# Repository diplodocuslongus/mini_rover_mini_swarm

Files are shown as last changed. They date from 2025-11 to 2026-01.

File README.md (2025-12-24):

# Mini rover mini swarm

Using the pololu romi platform to create a swarm of few rovers.
Documenting the assembly, setup and usage of some simple, basic and more or less cheap rover platform such as the pololu romi to be controlled by an autopilot (ex ardurover) and evolve in a swarm.

## Rover platform

For all options (pololu romi or alternatives):
- autopilot board compatible with the chosen autopilot (ardupilot or PX4), we chose the mateksys F405-WMO, the [h743-mini](https://www.mateksys.com/?portfolio=h743-mini) is fine too.

### Romi

BOM (can be adjusted)
- romi chassis
- [power distribution](https://www.pololu.com/product/3541) board or the [motor driver + power board](https://www.pololu.com/product/3543) or the [controller board](https://www.pololu.com/product/3544) 
- [encoder pair for romi motors ](https://www.pololu.com/product/3542)
- NiMH batteries
- motor driver (if not using the controller board)

[Assembly guide:](https://www.pololu.com/docs/0J68/all)

Other references:
- https://ardupilot.org/rover/docs/common-autopilots.html
- https://discuss.ardupilot.org/t/ardurover-with-the-pololu-romi/41991

### Cheap platform

Similar outcomes can be achieved with various degrees of success by using cheap platform, but they may be unrelieable especially when it comes to the wheel encoder parts. 

## autopilot

### control modes

The [follow mode](https://ardupilot.org/rover/docs/follow-mode.html) can be used for a basic swarm like behaviour, though it doesn't include any form of self-decision: vehicles follow each other and in order, with one vehicle in front.

### Firmware

This page says to use this firmware:
https://www.mateksys.com/?portfolio=f405-wmo#tab-id-2

https://firmware.ardupilot.org/Rover/stable/MatekF405-TE/

## connections

Power distribution board
By dfault the power distribution board supplies voltage from all the 6 batteries of the ROMI, this can be changed but having enough voltage is best to power directly the autopilot.

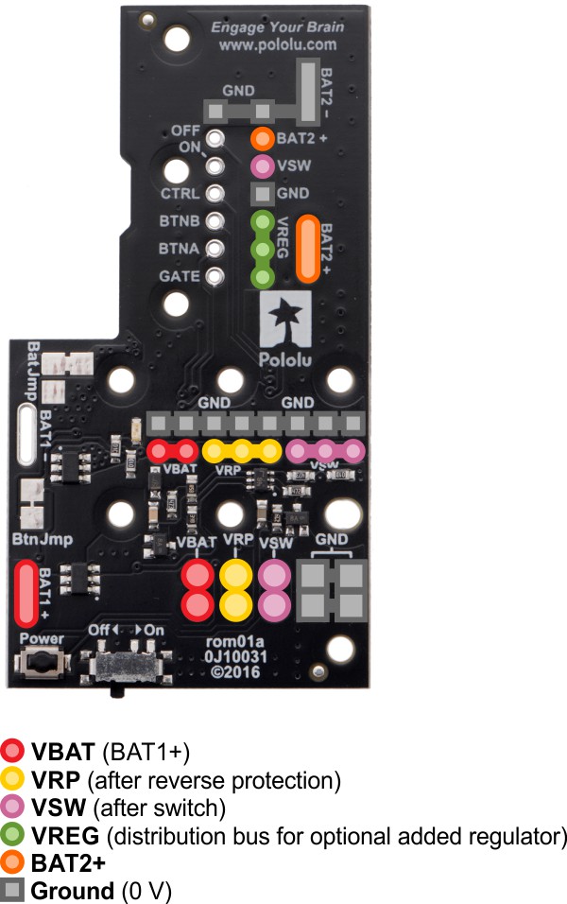
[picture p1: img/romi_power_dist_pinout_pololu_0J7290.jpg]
power_dist_pinout


**Wheel encoder.**

VCC can be 3.5 V to 18 V

*Important*
The Mateksys F405-WMO flight controller does not have physical, onboard pull-up resistors, neither does the wheel encoder for ROMI. They must be installed or the wheel encoder signal will be too weak for the FC to detect it.
Solder 4.7k resistor between the output A and B and VCC for each encoder.
That is, one 4.7k resistor from output A to VCC and another 4.7k from output B to VCC for left encoder, repeat for the right one.

https://ardupilot.org/rover/docs/wheel-encoder.html

Connect the encoder VCC to one of the Vx pin on the autopilot.

The AP we use has 3.3V logic levels but it is 5V tolerant.

Motor driver

It requires 2 separate supplies, one to the logic (1.8V ~ 7V) and one for the power to the motors (2~11V). The logic voltage can be obtained from the autopilot, or via a voltage converter.

Note that the motors are positioned in a mirror image of each other so if connecting everything exactly on the left and right, motors will spin in opposite directions when increasing the throttle. If this happens, simply inverse M1 with M2 on one of the encorder board (or on the driver output).
The same concept goes if motors are spinning in reverse (rover moving forward when it should move backward).

**RC receiver.**

A futaba receiver was used and pairing and connection varies depending on the RC brand and protocol.

This is an sbus based Rx, connect to the mateksys to the SBUS pin, and a 5V power pin such as Vx or the 4V5 pin which is powered when the FC is connected to USB to a computer.

## Autopilot setup

Calibrate the radio in QGC or MP.

Setup the various parameters

Everytime one or more parameters is set, the FC has to be rebooted in order for the parameter to be taken into account.
For example in a newly flashed FC, RELAYx_FUNCTION is set to 0 and no other RELAY related parameters will appear.
In order to access to other RELAY parameters such as RELAYx_PIN, etc, the RELAYx_FUNCTION has to be set and the FC rebooted.

We will use the motor driver in phase-enable mode (in motor driver language; ithis corresponds to "brushed with relay" in the ardupilot [wiki](https://ardupilot.org/rover/docs/common-brushed-motors.html#common-brushed-motors)), and the connections follows the schematic from pololu.
"Brushed With Relay” is for brushed motor drivers that use a relay pin to indicate whether it should rotate forward or backward. 

The type of control for the romi is called skid steering. The settings below are made for this.

https://ardupilot.org/rover/docs/rover-motor-and-servo-configuration.html#skid-steering

Summary of all settings

RELAY1_FUNCTION -> 5
RELAY1_PIN -> 50
RELAY2_FUNCTION -> 6
RELAY2_PIN -> 51

WENC_TYPE -> 1 (quadrature)
WENC2_TYPE -> 1 (quadrature)

# MOT_PWM_TYPE

MOT_PWM_TYPE -> 3 (BrushedWithRelay)

*SERVO*

Servo parameters dictates whether a given pin acts as PWM or GPIO.
They must be set properly.

See below for how to set them on a per-function basis.

*RELAY_FUNCTION*

Relay are used to select the rotation direction of the motors on the motor driver.
Search for relay in the search box of QGC or MP.
Set as follows:

RELAY1_FUNCTION -> 5
RELAY2_FUNCTION -> 6

For this to work we also have to set the corresponding servo function to GPIO:

SERVO7_FUNCTION -> -1 (GPIO)
SERVO8_FUNCTION -> -1 (GPIO)

Reboot

Then set relay pins:
RELAY1_PIN -> 56
RELAY2_PIN -> 57

[!] The value for these parameters is HW dependent, check the FC datasheet and double check with the hwdef.dat file corresponding to that particular FC.
Note also that these are connected to S1 and S2 pins on the FC. 
[!] it is adviced not to mix pins dedicated to GPIO (ex, relay function) and pins dedicated to PWM.

For the MatekSys F405-WMO, the corresponding hwdef.dat is [here](https://github.com/ArduPilot/ardupilot/blob/master/libraries/AP_HAL_ChibiOS/hwdef/MatekF405-TE/hwdef.dat)

*WENC (Wheel encoder)*

Related [ardurover doc](https://ardupilot.org/rover/docs/wheel-encoder.html).
set WENC_TYPE  to 1 (quadrature) and reboot the FC to enable other parameters and the second wheel encoder.

WENC_TYPE -> 1 (quadrature)

reboot so that more parameters and the second wheel encoder appears.

WENC2_TYPE -> 1 (quadrature)

Set the corresponding servo function to GPIO:

SERVO3_FUNCTION -> -1 (GPIO)
SERVO4_FUNCTION -> -1 (GPIO)
SERVO5_FUNCTION -> -1 (GPIO)
SERVO6_FUNCTION -> -1 (GPIO)

set EK3_SRC1_VELXY to 7 (WheelEncoder)

## command the rover with mavlink messages

### using mavproxy

Install mavproxy

Turn on the main power , plug the FC usb to the computer.

    mavproxy.py --master=/dev/ttyACM0 --baudrate=115200

Open with the console

    $ mavproxy.py --master=/dev/ttyACM0 --baudrate=115200 --console

To connect via an AP, see picoW AP code, use:

    mavproxy.py --master=udpout:192.168.4.1:14550

`192.168.4.1` is the picoW's IP address and `14550` the port for udp

Lots of messages will be shown in the console, which can be inconvienient when typing malink commands, so send these message to the gui console by typing:

    module load console

Or load mavproxy with the console module directly:

    mavproxy.py --master=udpout:192.168.4.1:14550 --console

Make sure EK3_SRC1_VELXY is set to 7 (to make use of wheel odometry)

Either in QGC or using a mavlink message:

params set ek3_src1_velxy 7 

(tip: tab completion works, and if the parameter's name is unsure, type:

`param set ek3_src1*`, which will show:

    EK3_SRC1_POSXY   0           # None
    EK3_SRC1_POSZ    0           # None
    EK3_SRC1_VELXY   7           # WheelEncoder
    EK3_SRC1_VELZ    0           # None
    EK3_SRC1_YAW     0           # None

We need to set the GPS origin:

    module load message
    message SET_GPS_GLOBAL_ORIGIN 0 -353621474 1491651746 600000 0

Change to guided mode and arm:

    mode guided
    arm throttle

Then send a move forward message:

    message SET_POSITION_TARGET_LOCAL_NED 0 0 0 7 3580 0.6 0 0 0 0 0 0 0 0 0 0

Simple test: spin the wheels for a given distance or velocity:

Ensure 

### using program (C or python)

A program is used to send specific commands.

Python:

1) connect to the pico W AP
2) connect to rover with :

    mavproxy.py --master=udpout:192.168.4.1:14550

3) in mavproxy, run:

        module load console
        module load message
        message SET_GPS_GLOBAL_ORIGIN 0 -353621474 1491651746 600000 0
        mode guided
        arm throttle

4) run the python script to move forward:
    
    py move_fwd.py

## send telemetry via a companion computer.

We chose the raspberry pi picoW for this.

We'll set up a full MAVLink communication between the rover and QGroundControl (QGC) using the Raspberry Pi Pico W as a UDP bridge.

- Integrate MAVLink into the Pico W code (to encode/decode MAVLink messages).
- Forward MAVLink messages between the flight controller (FC) and QGC via UDP.
- Ensure QGC is configured to connect to the Pico W's UDP endpoint.

## Useful references:

- [list of all rover parameters](https://ardupilot.org/rover/docs/parameters.html)
- 

## Abreviations

AP: AutoPilot (=FC)
FC: Flight controller

# Debugging

## general guidelines

Monitor some parameters in mavproxy

    watch name_of_the_parameter

stop watching (this will stop watching everything):

    watch clear 

For one shot watching all the parameters:

    status 

For a single parameter, here to see the RC channels as read by the FC (needs RC on and connected of course to see a change):

    status RC_CHANNELS

## rover moves backward

General guideline: leave the RC channels as they are on the RC itself, i.e. don't reverse them there, and reverse what is required on the FC parmaeters.

Reverse in AP if needed (RC3 is throttle here, check setting)

    param set RC3_REVERSED 1 

## rover moves too fast

Check the following FC parameters:

    param show CRUISE_SPEED
    param show WP_SPEED

Lower the values for CRUISE_SPEED and WP_SPEED (values are in m/s).

## Rover spinning on itself

- check motor direction
- `SERVOx_REVERSE`: normal or reversed? (x = 1 and 2 in this setup)
- check if RC can normally control the Rover
-
Check the values of the steering rate controller (ex, from mavproxy)

    param show ATC_STR_RAT_*
    GUIDED> ATC_STR_RAT_D    0.0
    ATC_STR_RAT_D_FF 0.0
    ATC_STR_RAT_FF   0.20000000298023224
    ATC_STR_RAT_FLTD 0.0
    ATC_STR_RAT_FLTE 10.0
    ATC_STR_RAT_FLTT 0.0
    ATC_STR_RAT_I    0.20000000298023224
    ATC_STR_RAT_IMAX 1.0
    ATC_STR_RAT_MAX  120.0
    ATC_STR_RAT_P    0.20000000298023224
    ATC_STR_RAT_PDMX 0.0
    ATC_STR_RAT_SMAX 0.0

Some parameters that affect the turn and turn rate:

    param set ATC_STR_RAT_MAX 30
    param set ATC_STR_RAT_FF 0.3
    param set MOT_SLEWRATE 60
    param set MOT_THR_MIN 10

## rover tends to veer on one side when moving forward

Adjust with SERVO1_TRIM andi/or SERVO2_TRIM.

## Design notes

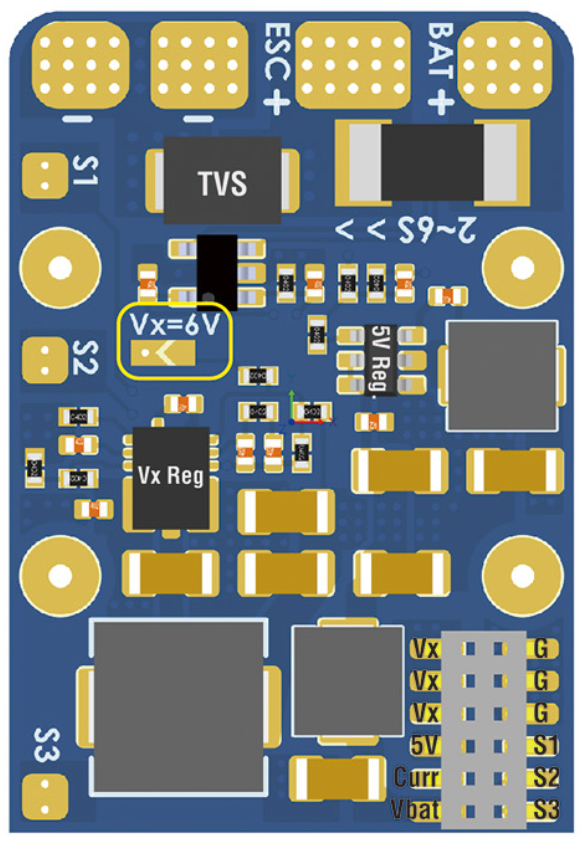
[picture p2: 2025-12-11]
img/mateksysF405_wmo_bottom.png

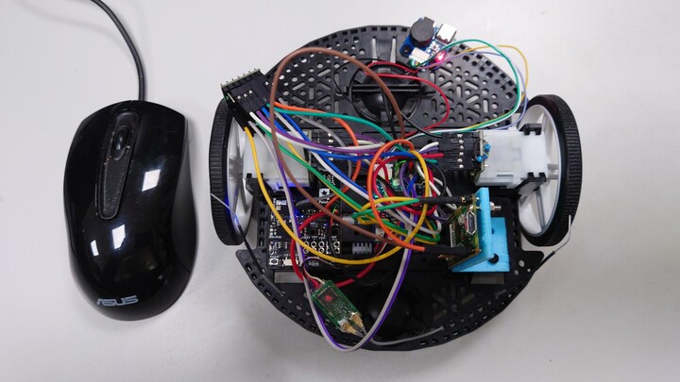
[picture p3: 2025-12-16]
img/romi_rover_picoW.jpg

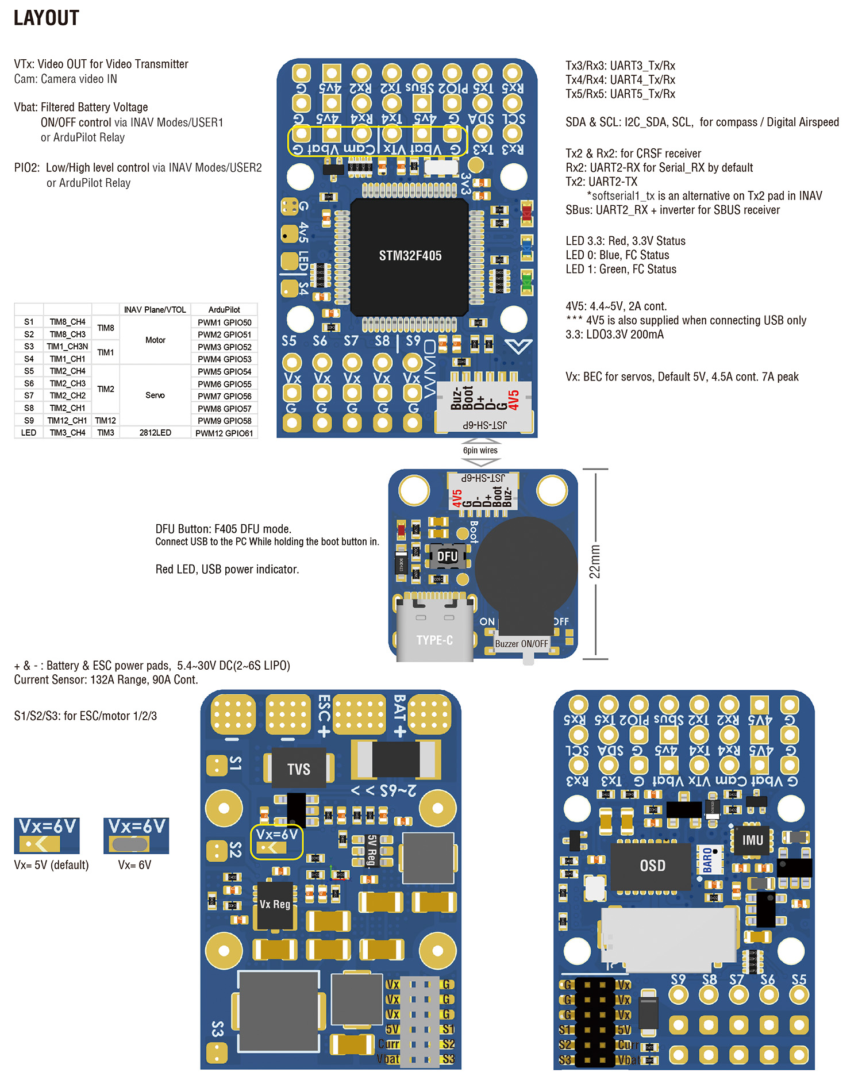
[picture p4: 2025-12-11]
img/mateksysF405-WMO_layout.jpg

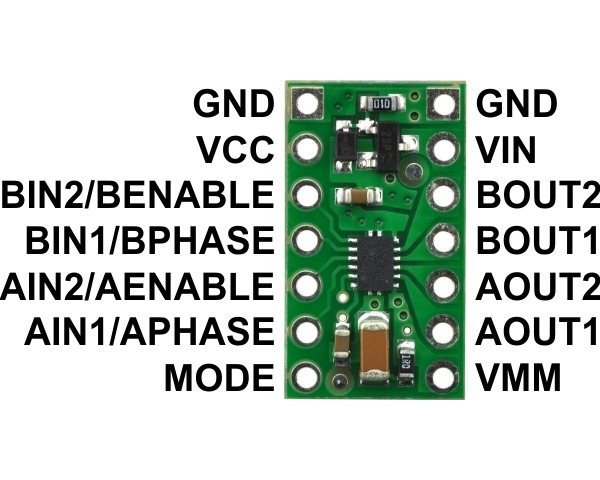
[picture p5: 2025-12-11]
img/pololu_motor_driver_drv8835.jpg

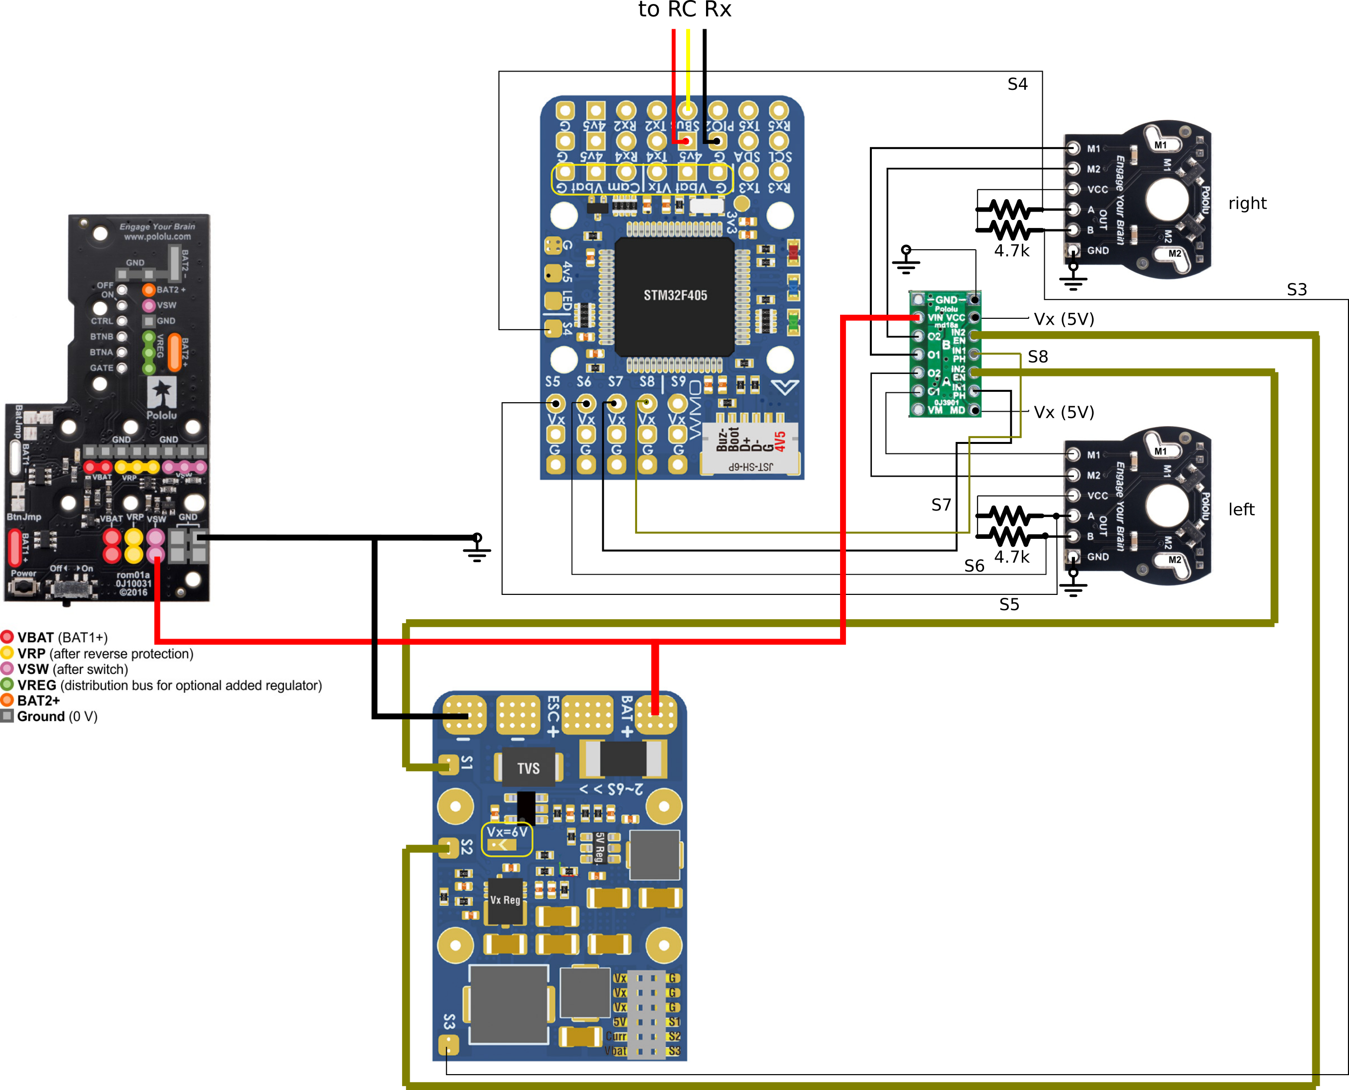
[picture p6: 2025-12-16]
img/all_connections_no_picow.png

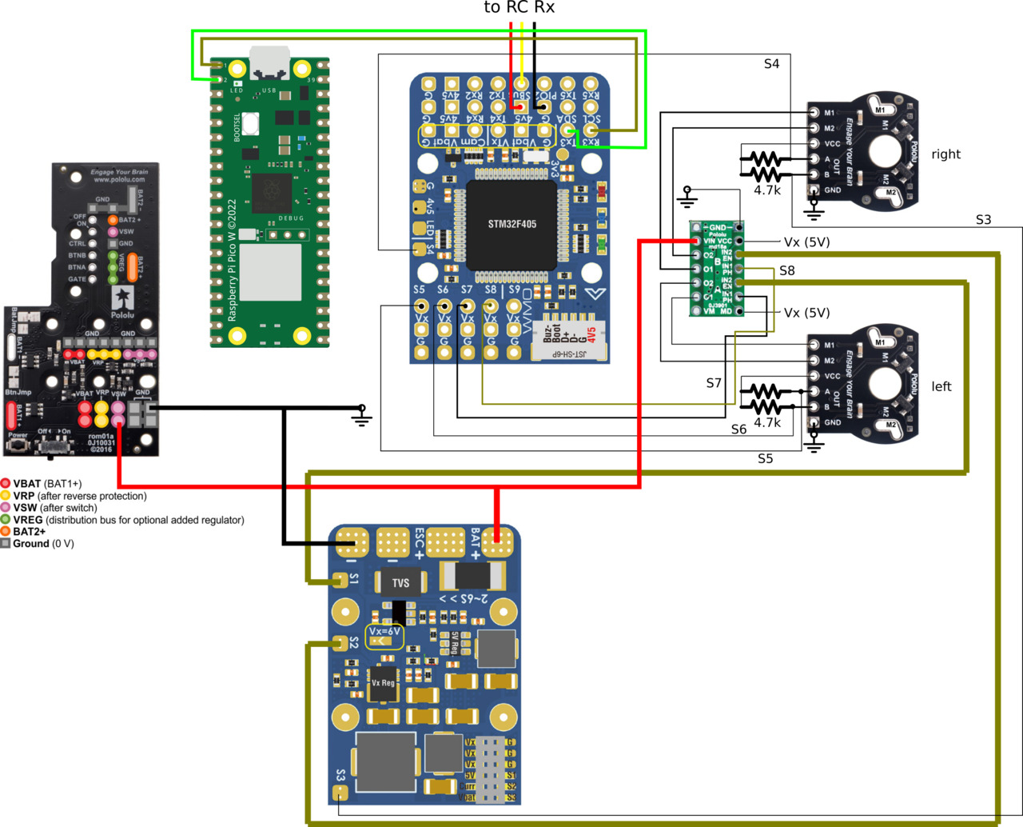
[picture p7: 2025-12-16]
img/all_connections_picow.jpg

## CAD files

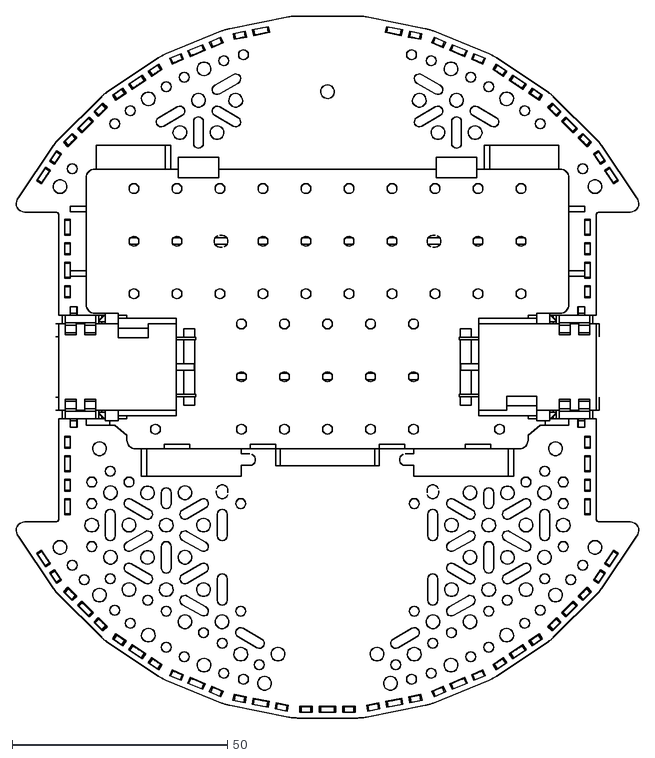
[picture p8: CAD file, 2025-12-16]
img/romi_chassis_toponly_nowheels_fromdxf.dxf
144.8 x 163.2

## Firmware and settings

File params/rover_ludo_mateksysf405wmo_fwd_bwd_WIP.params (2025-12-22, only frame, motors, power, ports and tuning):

1	1	ATC_SPEED_D	0.000000000000000000	9
1	1	ATC_SPEED_D_FF	0.000000000000000000	9
1	1	ATC_SPEED_FF	0.000000000000000000	9
1	1	ATC_SPEED_FLTD	0.000000000000000000	9
1	1	ATC_SPEED_FLTE	10.000000000000000000	9
1	1	ATC_SPEED_FLTT	0.000000000000000000	9
1	1	ATC_SPEED_I	0.200000002980232239	9
1	1	ATC_SPEED_IMAX	1.000000000000000000	9
1	1	ATC_SPEED_P	0.200000002980232239	9
1	1	ATC_SPEED_PDMX	0.000000000000000000	9
1	1	ATC_SPEED_SMAX	0.000000000000000000	9
1	1	ATC_STR_ACC_MAX	20.000000000000000000	9
1	1	ATC_STR_ANG_P	2.000000000000000000	9
1	1	ATC_STR_RAT_D	0.000000000000000000	9
1	1	ATC_STR_RAT_D_FF	0.000000000000000000	9
1	1	ATC_STR_RAT_FF	0.200000002980232239	9
1	1	ATC_STR_RAT_FLTD	0.000000000000000000	9
1	1	ATC_STR_RAT_FLTE	10.000000000000000000	9
1	1	ATC_STR_RAT_FLTT	0.000000000000000000	9
1	1	ATC_STR_RAT_I	0.000000000000000000	9
1	1	ATC_STR_RAT_IMAX	1.000000000000000000	9
1	1	ATC_STR_RAT_MAX	120.000000000000000000	9
1	1	ATC_STR_RAT_P	0.200000002980232239	9
1	1	ATC_STR_RAT_PDMX	0.000000000000000000	9
1	1	ATC_STR_RAT_SMAX	0.000000000000000000	9
1	1	BATT2_MONITOR	0	2
1	1	BATT3_MONITOR	0	2
1	1	BATT4_MONITOR	0	2
1	1	BATT5_MONITOR	0	2
1	1	BATT6_MONITOR	0	2
1	1	BATT7_MONITOR	0	2
1	1	BATT8_MONITOR	0	2
1	1	BATT9_MONITOR	0	2
1	1	BATT_AMP_OFFSET	0.000000000000000000	9
1	1	BATT_AMP_PERVLT	66.699996948242187500	9
1	1	BATT_ARM_MAH	0	6
1	1	BATT_ARM_VOLT	0.000000000000000000	9
1	1	BATT_CAPACITY	3300	6
1	1	BATT_CRT_MAH	0.000000000000000000	9
1	1	BATT_CRT_VOLT	0.000000000000000000	9
1	1	BATT_CURR_PIN	15	2
1	1	BATT_FS_CRT_ACT	0	2
1	1	BATT_FS_LOW_ACT	0	2
1	1	BATT_FS_VOLTSRC	0	2
1	1	BATT_LOW_MAH	0.000000000000000000	9
1	1	BATT_LOW_TIMER	10	2
1	1	BATT_LOW_VOLT	0.000000000000000000	9
1	1	BATT_MONITOR	4	2
1	1	BATT_OPTIONS	0	6
1	1	BATT_SERIAL_NUM	-1	6
1	1	BATT_VLT_OFFSET	0.000000000000000000	9
1	1	BATT_VOLT_MULT	21.000000000000000000	9
1	1	BATT_VOLT_PIN	14	2
1	1	FLTMODE_GCSBLOCK	0	6
1	1	FRAME_CLASS	1	2
1	1	FRAME_TYPE	0	2
1	1	INS_GYRO_FILTER	4	4
1	1	INS_HNTCH_ENABLE	0	2
1	1	MOT_PWM_FREQ	16	2
1	1	MOT_PWM_TYPE	3	2
1	1	MOT_SAFE_DISARM	0	2
1	1	MOT_SLEWRATE	100	4
1	1	MOT_SPD_SCA_BASE	1.000000000000000000	9
1	1	MOT_STR_THR_MIX	0.500000000000000000	9
1	1	MOT_THR_MAX	100	2
1	1	MOT_THR_MIN	0	2
1	1	MOT_THST_ASYM	1.000000000000000000	9
1	1	MOT_THST_EXPO	0.000000000000000000	9
1	1	MOT_VEC_ANGLEMAX	0.000000000000000000	9
1	1	SERIAL0_BAUD	115	6
1	1	SERIAL0_PROTOCOL	2	2
1	1	SERIAL1_BAUD	57	6
1	1	SERIAL1_OPTIONS	0	4
1	1	SERIAL1_PROTOCOL	2	2
1	1	SERIAL2_BAUD	57	6
1	1	SERIAL2_OPTIONS	0	4
1	1	SERIAL2_PROTOCOL	2	2
1	1	SERIAL3_BAUD	57	6
1	1	SERIAL3_OPTIONS	0	4
1	1	SERIAL3_PROTOCOL	2	2
1	1	SERIAL4_BAUD	230	6
1	1	SERIAL4_OPTIONS	0	4
1	1	SERIAL4_PROTOCOL	5	2
1	1	SERIAL5_BAUD	57	6
1	1	SERIAL5_OPTIONS	0	4
1	1	SERIAL5_PROTOCOL	-1	2
1	1	SERIAL6_BAUD	57	6
1	1	SERIAL6_OPTIONS	0	4
1	1	SERIAL6_PROTOCOL	-1	2
1	1	SERVO1_FUNCTION	73	4
1	1	SERVO1_MAX	1900	4
1	1	SERVO1_MIN	900	4
1	1	SERVO1_REVERSED	1	2
1	1	SERVO1_TRIM	900	4
1	1	SERVO2_FUNCTION	74	4
1	1	SERVO2_MAX	1900	4
1	1	SERVO2_MIN	900	4
1	1	SERVO2_REVERSED	1	2
1	1	SERVO2_TRIM	900	4
1	1	SERVO3_FUNCTION	-1	4
1	1	SERVO3_MAX	1900	4
1	1	SERVO3_MIN	1100	4
1	1	SERVO3_REVERSED	0	2
1	1	SERVO3_TRIM	1500	4
1	1	SERVO4_FUNCTION	-1	4
1	1	SERVO4_MAX	1900	4
1	1	SERVO4_MIN	1100	4
1	1	SERVO4_REVERSED	0	2
1	1	SERVO4_TRIM	1500	4
1	1	SERVO5_FUNCTION	-1	4
1	1	SERVO5_MAX	1900	4
1	1	SERVO5_MIN	1100	4
1	1	SERVO5_REVERSED	0	2
1	1	SERVO5_TRIM	1500	4
1	1	SERVO6_FUNCTION	-1	4
1	1	SERVO6_MAX	1900	4
1	1	SERVO6_MIN	1100	4
1	1	SERVO6_REVERSED	0	2
1	1	SERVO6_TRIM	1500	4
1	1	SERVO7_FUNCTION	-1	4
1	1	SERVO7_MAX	1900	4
1	1	SERVO7_MIN	1100	4
1	1	SERVO7_REVERSED	0	2
1	1	SERVO7_TRIM	1500	4
1	1	SERVO8_FUNCTION	-1	4
1	1	SERVO8_MAX	1900	4
1	1	SERVO8_MIN	1100	4
1	1	SERVO8_REVERSED	0	2
1	1	SERVO8_TRIM	1500	4
1	1	SERVO9_FUNCTION	0	4
1	1	SERVO9_MAX	1900	4
1	1	SERVO9_MIN	1100	4
1	1	SERVO9_REVERSED	0	2
1	1	SERVO9_TRIM	1500	4

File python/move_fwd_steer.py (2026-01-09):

# move forward and/or steer
from pymavlink import mavutil
import time

# Connect to the autopilot via UDP (PicoW)
master = mavutil.mavlink_connection('udp:192.168.4.1:14550', source_system=255, input=False)

# Wait for the heartbeat
print("Waiting for heartbeat...")
master.wait_heartbeat(timeout = 5)
print(f"Heartbeat received from system (system {master.target_system} component {master.target_component})")

def send_command(command, param1=0, param2=0, param3=0, param4=0, param5=0, param6=0, param7=0):
    master.mav.command_long_send(
        master.target_system,
        master.target_component,
        command,
        0,  # confirmation
        param1, param2, param3, param4, param5, param6, param7
    )
    ack = master.recv_match(type='COMMAND_ACK', blocking=True, timeout=3)
    if ack is not None:
        print(f"Command {command} acknowledged: {mavutil.mavlink.enums['MAV_RESULT'][ack.result].name}")
        return ack.result == mavutil.mavlink.MAV_RESULT_ACCEPTED
    else:
        print(f"Command {command} not acknowledged")
        return False

def set_gps_global_origin(latitude, longitude, altitude):
    master.mav.command_long_send(
        master.target_system,
        master.target_component,
        mavutil.mavlink.MAV_CMD_DO_SET_HOME,
        0,  # Confirmation
        1,  # Use current position: 1 (true)
        0, 0, 0,  # Unused parameters
        latitude / 1e7,  # Latitude in degrees (scaled by 1e7)
        longitude / 1e7,  # Longitude in degrees (scaled by 1e7)
        altitude  # Altitude in meters
    )

def arm():
    print("Arming...")
    if not send_command(mavutil.mavlink.MAV_CMD_COMPONENT_ARM_DISARM, 1):
        print("Failed to arm. Check safety switch, RC, and sensors.")
        return False
    return True

def disarm():
    print("Disarming...")
    if not send_command(mavutil.mavlink.MAV_CMD_COMPONENT_ARM_DISARM, 0):
        print("Failed to disarm. Check safety switch, RC, and sensors.")
        return False
    return True

def print_wheel_distance(duration):
    end_time = time.time() + duration
    while time.time() < end_time:
        msg = master.recv_match(type='WHEEL_DISTANCE', blocking=True, timeout=1)
        if msg is not None:
            print(f"Wheel distances: {msg.distance}")

def drive_forward(distance, speed=0.1):
    # Time = Distance / Speed
    duration = distance / speed
    print(f"Driving forward {distance}m...")
    send_vel(speed, 0, 0, duration, 10)
    # Give the EKF a moment to settle
    time.sleep(0.5)

def turn_rate_angle(turn_rate_deg = 30,turn_angle = 90, direction ="left"):
    # We use Mask 1511.
    # The last parameter is yaw_rate in radians/sec.
    # 20 degrees/sec = ~0.35 rad/s
    # turn_rate_deg = 30 #30
    turn_rate_rad = turn_rate_deg * 3.14 / 180.0
    yaw_rate_rad = turn_rate_rad if direction == "right" else -turn_rate_rad
    # Duration to get 90 degrees at 20 deg/s is 4.5 seconds
    duration = turn_angle / turn_rate_deg  + 0.15
    
    print("Turning left 90 degrees...")
    end_time = time.time() + duration
    while time.time() < end_time:
        master.mav.set_position_target_local_ned_send(
            0, master.target_system, master.target_component,
            mavutil.mavlink.MAV_FRAME_BODY_NED,
            1511,       # Mask 1511 (Uses Vel X and Yaw Rate)
            0, 0, 0,    # Position
            0, 0, 0,    # Velocity (Set to 0 to pivot in place)
            0, 0, 0,    # Acceleration
            0, yaw_rate_rad # Negative is usually Left in ArduPilot
        )
        time.sleep(0.1)
    
    # Explicit Stop
    send_vel(0, 0, 0, 0.5, 10)
    time.sleep(0.5)

def turn_left_90( direction ="left"):
    # We use Mask 1511.
    # The last parameter is yaw_rate in radians/sec.
    # 20 degrees/sec = ~0.35 rad/s
    turn_rate_deg = 30 #30
    turn_rate_rad = turn_rate_deg * 3.14 / 180.0
    yaw_rate_rad = turn_rate_rad if direction == "right" else -turn_rate_rad
    # Duration to get 90 degrees at 20 deg/s is 4.5 seconds
    duration = 90 / turn_rate_deg  + 0.15
    
    print("Turning left 90 degrees...")
    end_time = time.time() + duration
    while time.time() < end_time:
        master.mav.set_position_target_local_ned_send(
            0, master.target_system, master.target_component,
            mavutil.mavlink.MAV_FRAME_BODY_NED,
            1511,       # Mask 1511 (Uses Vel X and Yaw Rate)
            0, 0, 0,    # Position
            0, 0, 0,    # Velocity (Set to 0 to pivot in place)
            0, 0, 0,    # Acceleration
            0, yaw_rate_rad # Negative is usually Left in ArduPilot
        )
        time.sleep(0.1)
    
    # Explicit Stop
    send_vel(0, 0, 0, 0.5, 10)
    time.sleep(0.5)



# Set GPS origin
print(f"Setting gps origin")
# set_gps_global_origin(-247743070, 1210455730, 100) # bg 51
# set_gps_global_origin(-353621474, 1491651746, 600) # desert
# time.sleep(1)  # Wait for the command to be processed
print(f"Done.")

# Arm the rover
# if not arm():
#     exit(1)

# Wait a moment for mode change
time.sleep(1)

# Send movement command: 1m forward at 0.2 m/s (adjust sign if wheels spin backward)
print("Sending movement command...")
def send_pos(pos):
    master.mav.set_position_target_local_ned_send(
        0,  # time_boot_ms
        master.target_system,
        master.target_component,
        mavutil.mavlink.MAV_FRAME_BODY_NED,
        # mavutil.mavlink.MAV_FRAME_LOCAL_NED,
        0b110111111000,  # type_mask: Use position (x) and velocity (vx)
        pos, 0, 0,  # x, y, z positions (meters)
        0, 0, 0,  # x, y, z velocities (m/s)
        0, 0, 0,  # x, y, z accelerations (not used)
        0, 0  # yaw, yaw_rate (not used)
    )
def send_pos_vel(pos,vel):
    master.mav.set_position_target_local_ned_send(
        0,  # time_boot_ms
        master.target_system,
        master.target_component,
        mavutil.mavlink.MAV_FRAME_BODY_NED,
        # mavutil.mavlink.MAV_FRAME_LOCAL_NED,
        0b110111100111,  # type_mask: Use position (x) and velocity (vx)
        pos, 0, 0,  # x, y, z positions (meters)
        vel, 0, 0,  # x, y, z velocities (m/s)
        0, 0, 0,  # x, y, z accelerations (not used)
        0, 0  # yaw, yaw_rate (not used)
    )
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

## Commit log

2025-11-26 assembly notes
2025-12-04 note on encoder, driver, WIP
2025-12-10 parameters and notes
    [rover_ludo_mateksysf405wmo.params]
2025-12-16 drawings, circuit diagram, notes
    [mav.parm]
2025-12-16 python move forward
    [mav.parm, romi_chassis_toponly_nowheels_fromdxf.dxf]
2025-12-16 python move forward, notes
    [mav.parm]
2025-12-18 still spinning, changed ATC and more params, adjust send_vel...
    [mav.parm]
2025-12-19 hope i m not messing up
    [mav.parm]
2025-12-19 new set of params, adjust PID, rectangle trajectory
    [rover_ludo_mateksysf405wmo_forguided_ok.params]
2025-12-22 adjust param and schematic
    [rover_ludo_mateksysf405wmo_fwd_bwd_WIP.params]
2026-01-02 fine tune steering
